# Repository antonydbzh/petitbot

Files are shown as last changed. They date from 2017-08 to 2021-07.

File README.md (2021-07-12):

# Le Petit Bot
1. Le Petit Bot c'est un robot, un programme, des logiciels pour commander Petit Bot et un programme pédagogique.
2. Le Petit Bot c'est un matériel facile à assembler par des jeunes à partir de 8 ans
3. Le Petit Bot ne coûte pas plus de 15 euros.
4. Un tutoriel détaillé est disponible sur [Wikidébrouillard](https://www.wikidebrouillard.org/wiki/Fabriquez_votre_PetitBot)

## Matériel
Le petit bot se compose :
* 2 servomoteurs à rotation continue
* 1 Wemos D1 Mini
* des fils dupont
* un système d'alimentation électrique (batterie 5V, support pour 4 piles AA - LR6,...).
* un interrupteur

En suite à vous de bricoler un plateforme, des roues, etc.
En carton, bouchon de bouteille, etc...

## Installation
L'installation de base consiste à changer le programme sur un wemos D1 mini avec l'IDE Arduino.
Puis de monter un robot à deux roues.
Puis, à la mise sus tension vous pouvez le controler via une page web à l'URL http://192.168.4.1
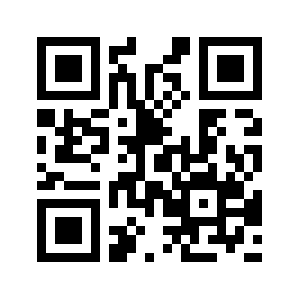
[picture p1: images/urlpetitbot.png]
QRCode de l'URL


## Usage
Le programme donne la capacité au petit bot d'être piloté depuis une page web.
il peut ainsi être piloté par [le logiciel SNAP! de l'Université de Californie à Berkeley](http://snap.berkeley.edu/).

## Contributing

1. Fork it!
2. Create your feature branch: `git checkout -b my-new-feature`
3. Commit your changes: `git commit -am 'Add some feature'`
4. Push to the branch: `git push origin my-new-feature`
5. Submit a pull request :D

## History

TODO: Write history

## Credits

Julien Rat - Les petits débrouillards
Antony Auffret - Les petits débrouillards
Et bien d'autres avant et après, un peu partout.
Ce programme est inspire de : http://www.esp8266.com/viewtopic.php?f=29&t=6419#sthash.gd1tJhwU.dpuf

## License

CC-By-Sa

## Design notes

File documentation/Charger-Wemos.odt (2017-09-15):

## Charger le programme sur le Wemos avec le logiciel Arduino

Pour programmer le wemos, nous utilisons le logiciel Arduino.

Nous devons ajouter quels outils complémentaires à ce logiciel pour deux raisons :

- Lui donner les capacité de gérer la carte Wemos D1 mini.
- Le doter de « bibliothèques » pour gérer le Wifi et les capteurs.

Attention en anglais le terme « librairies » est un faux-ami. Il se traduit par « bibliothèques ». Les bibliothèques sont des fichiers de code qu'il serait laborieux de retaper à chaque fois qu'on en a besoin.

### Ajouter les bibliothèques nécessaires

Pour le petit Bot nous avons besoin des bibliothèques suivantes :

- Servo.h

ATTENTION : Si il manque des bibliothèques, le logiciel Arduino refusera de charger le programme et renverra un message d'erreur. Ce message d'erreur vous indique quelle bibliothèque manque.

Pour installer les bibliothèques, il existe plusieurs manière. Le logiciel vous aide directement à installer les bibliothèques. Pour le cas ou certaines ne serait pas disponibles, essayez la seconde méthode.

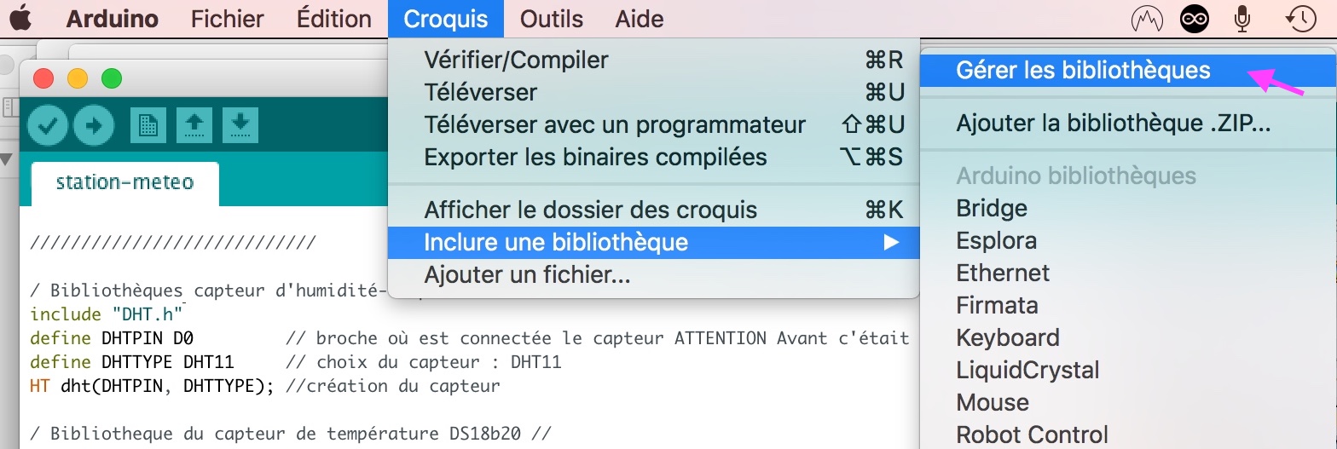
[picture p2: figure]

Commencez par celle-ci : ouvrez le logiciel Arduino puis allez dans Croquis → inclure une bibliothèque → gérer les bibliothèques

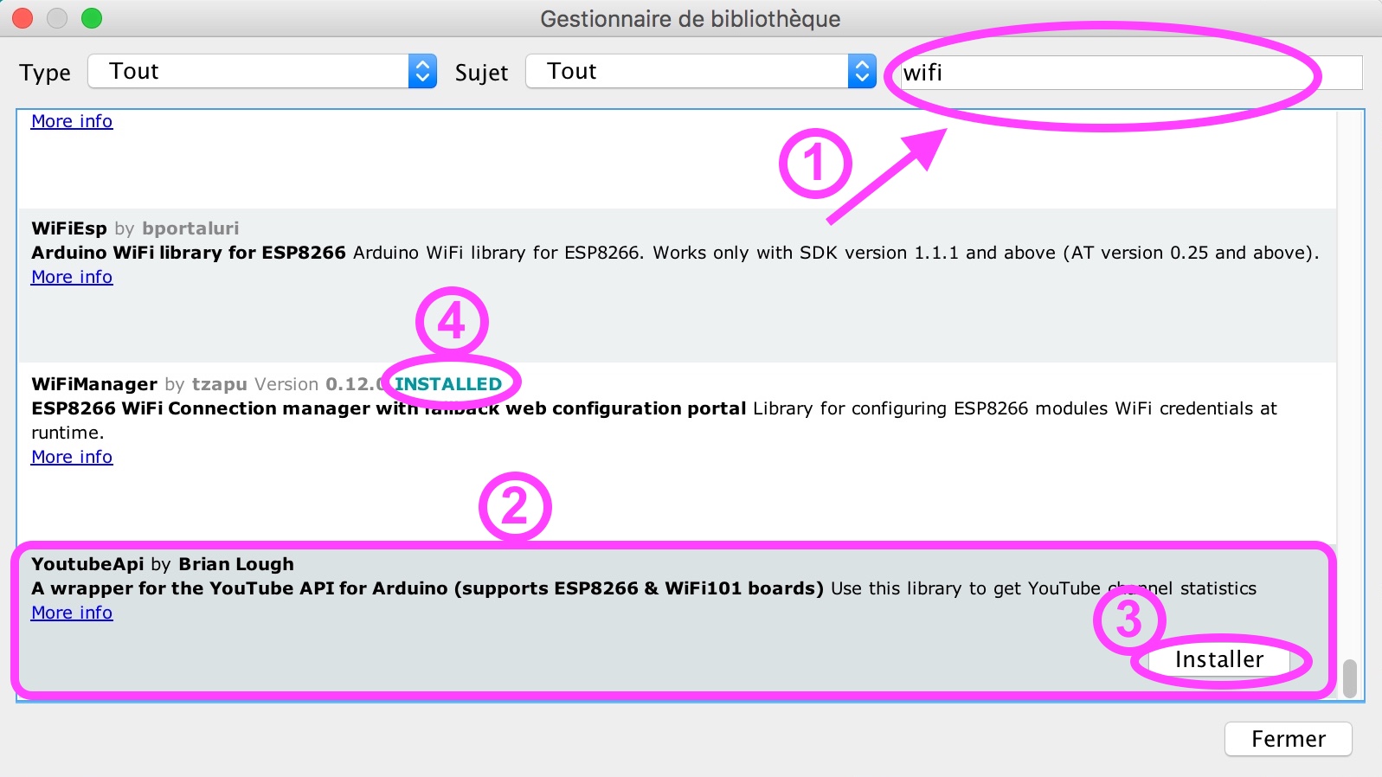
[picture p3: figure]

La fenêtre de gestion des bibliothèques s'ouvre :

1. Recherchez votre bibliothèque.
2. Cliquez la bibliothèque recherchée, « installer » apparaît.
3. Cliquez sur « installer »
4. Votre bibliothèque apparaît comme installée.

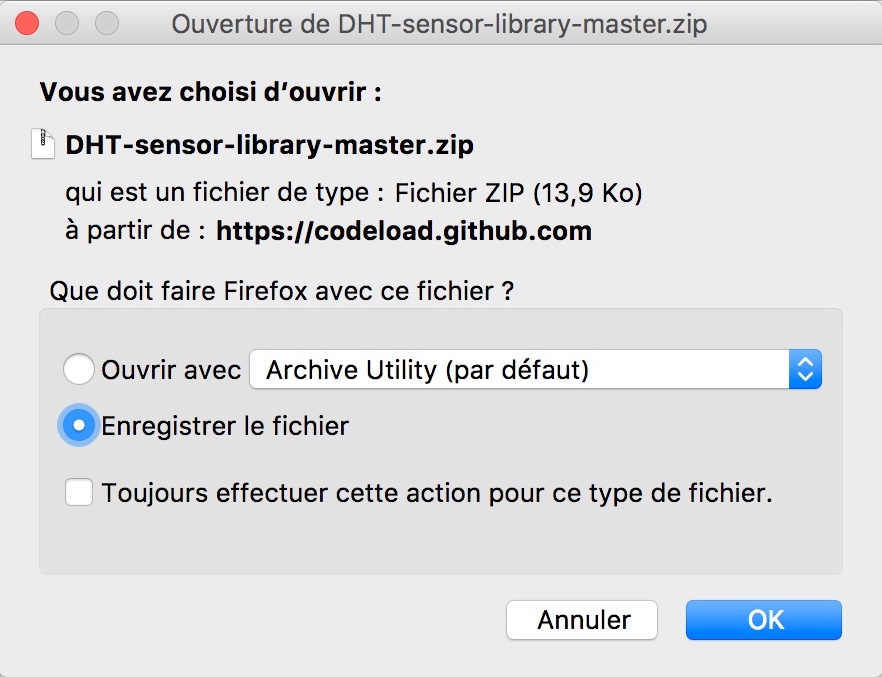
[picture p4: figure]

La seconde méthode :

Cliquez sur le lien donné plus haut pour télécharger la bibliothèque. Par exemple la bibliothèque qui permet de gérer les capteurs DHT.

https://github.com/adafruit/DHT-sensor-library/archive/master.zip

Votre navigateur vous propose de l'enregistrer, vous le faite, sur votre bureau par exemple.

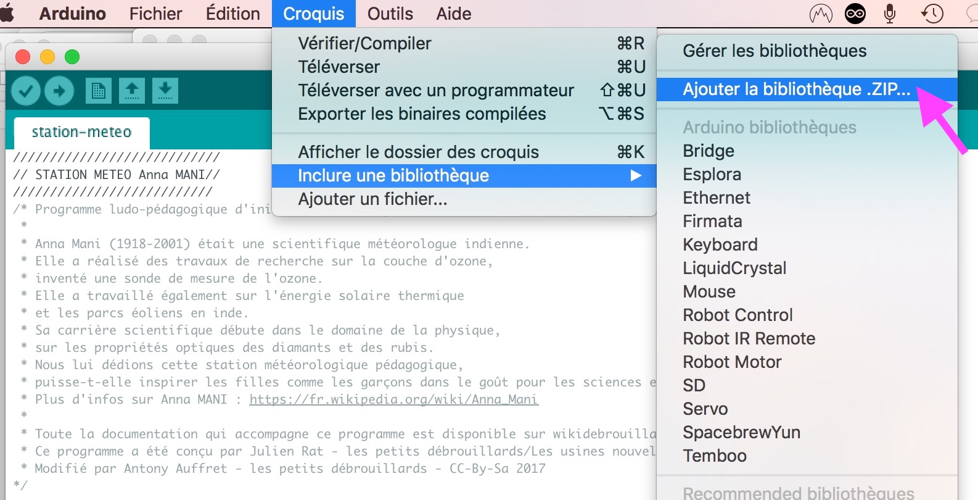
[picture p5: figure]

Ensuite, vous allez ajouter cette bibliothèque dans le logiciel Arduino.

Cliquez sur Croquis → inclure une bibliothèque → Ajouter la bibliothèque.ZIP

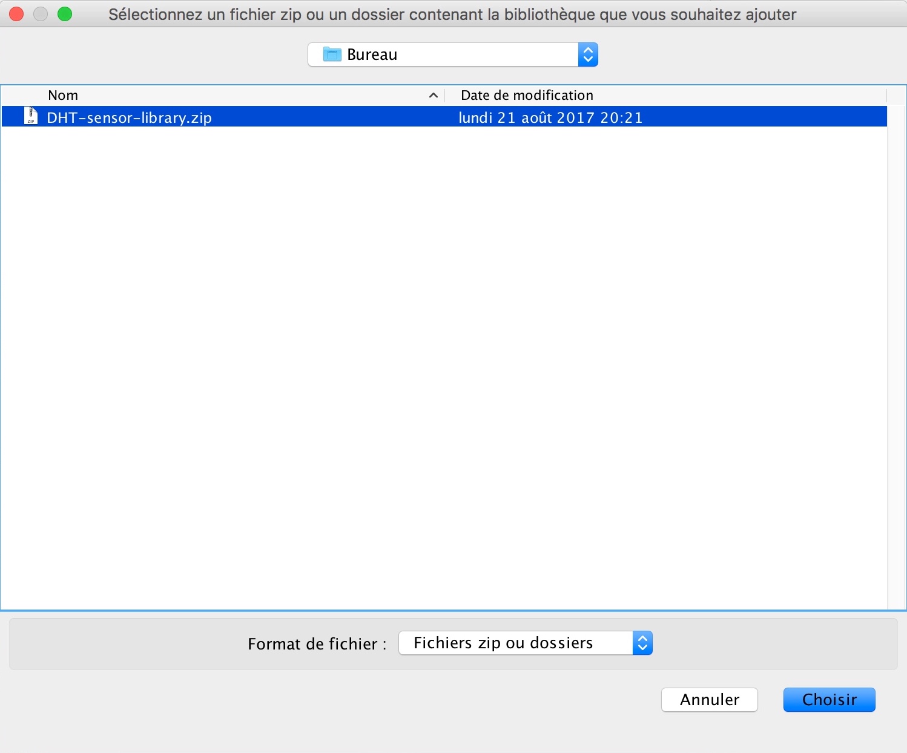
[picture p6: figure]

Une fenêtre de recherche s'ouvre.

Sélectionnez la bibliothèque, cliquez sur Choisir

C'est fait !

### Télécharger le programme sur le Wemos

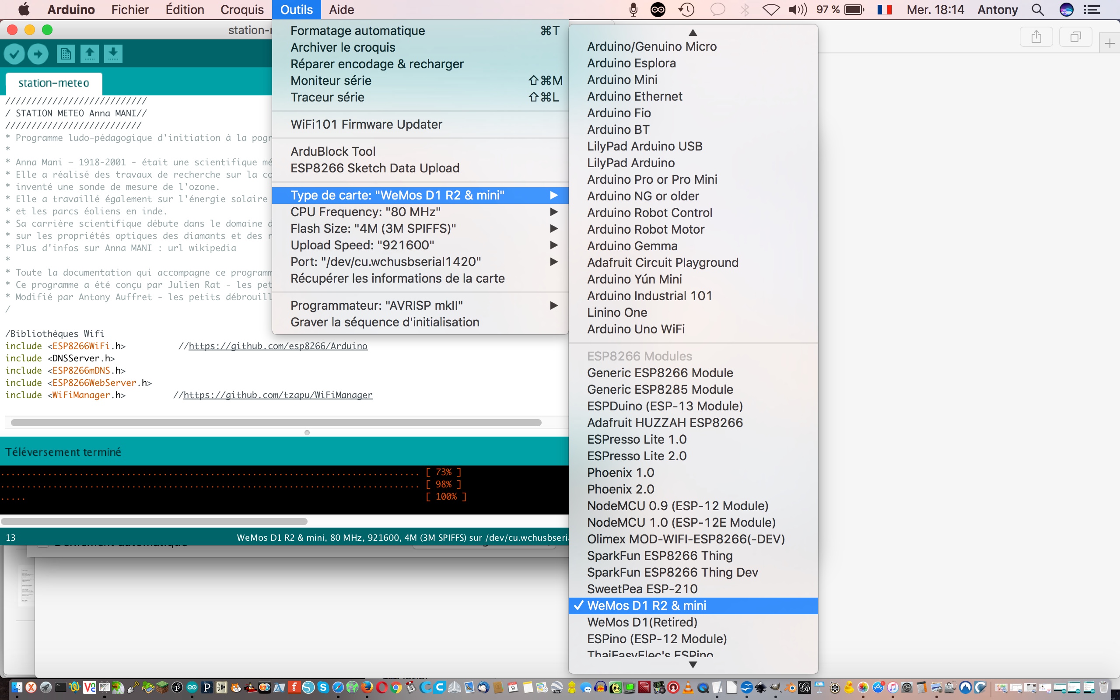
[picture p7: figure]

Ouvrez votre logiciel Arduino

Branchez le Wemos.

Choisissez le bon type de carte.

ATTENTION !

Il faut que vous ayez configuré le logiciel Arduino pour qu'il puisse gérer les cartes Wemos (Un tutoriel en se sens est disponible).

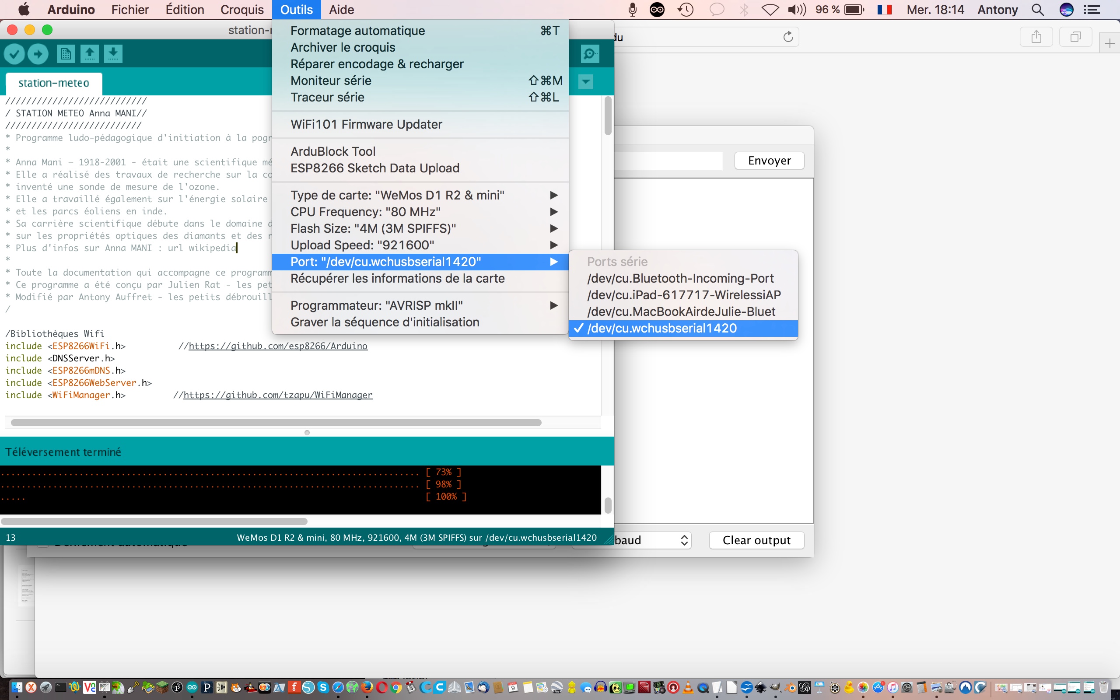
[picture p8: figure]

Choisissez le port.

Si le port du Wemos n'apparait pas, il y a plusieurs causes possibles :

- Les pilotes du Wemos ne sont pas installé.
- Le câble utilisé n'est pas bon (il existe des câbles USB-Micro USB qui ne font pas circuler les données (ceux des chargeurs simples par exemple)).

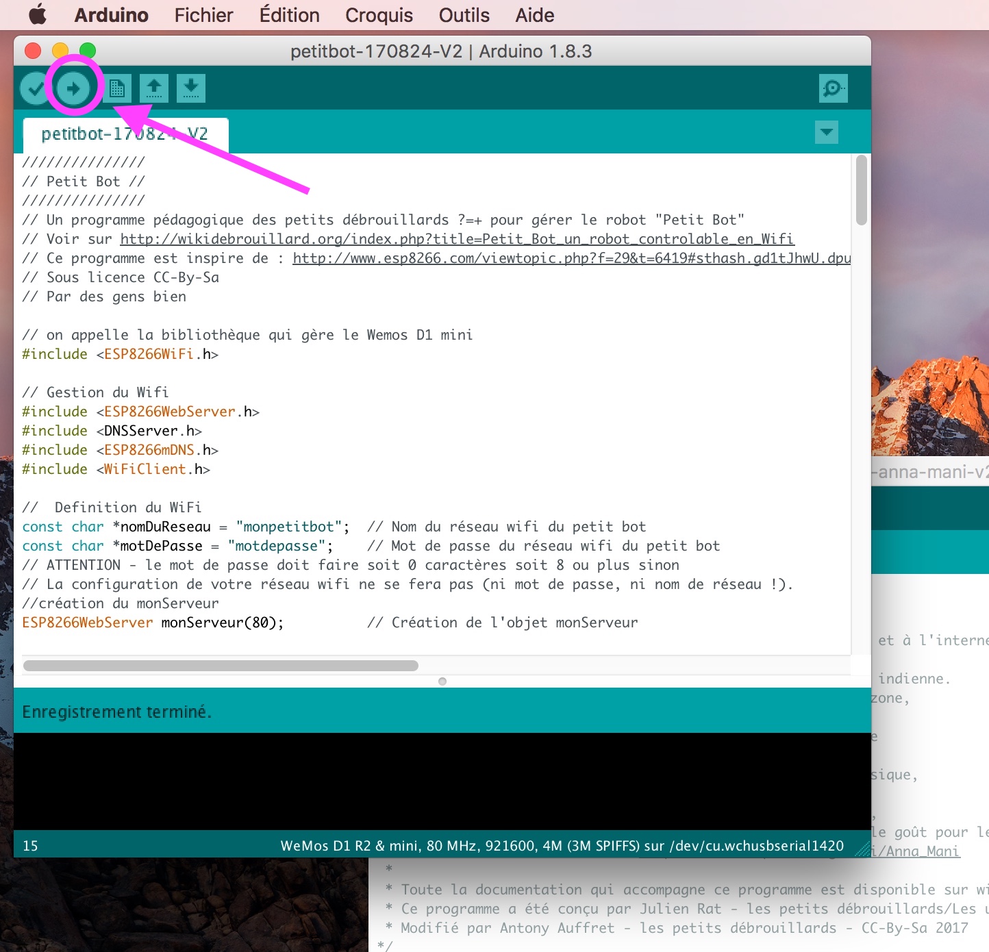
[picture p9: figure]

Téléversez le programme « petitbot » dans votre Wemos.

Si le téléchargement ne fonctionne pas essayez d'appuyer sur le bouton « reset » du Wemos.

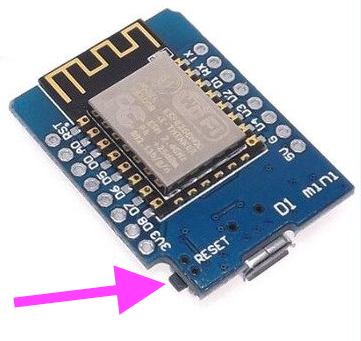
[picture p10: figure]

Une fois le programme chargé, le petit bot est prêt à servir.

Le petit Bot - 2017

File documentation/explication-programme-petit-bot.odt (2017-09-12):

//////////////////////

// Petit Bot //

//////////////////////

// Un programme pédagogique des petits débrouillards ?=+ pour gérer le robot "Petit Bot"

// Voir sur http://wikidebrouillard.org/index.php?title=Petit_Bot_un_robot_controlable_en_Wifi

// Ce programme est inspire de : http://www.esp8266.com/viewtopic.php?f=29&t=6419#sthash.gd1tJhwU.dpuf

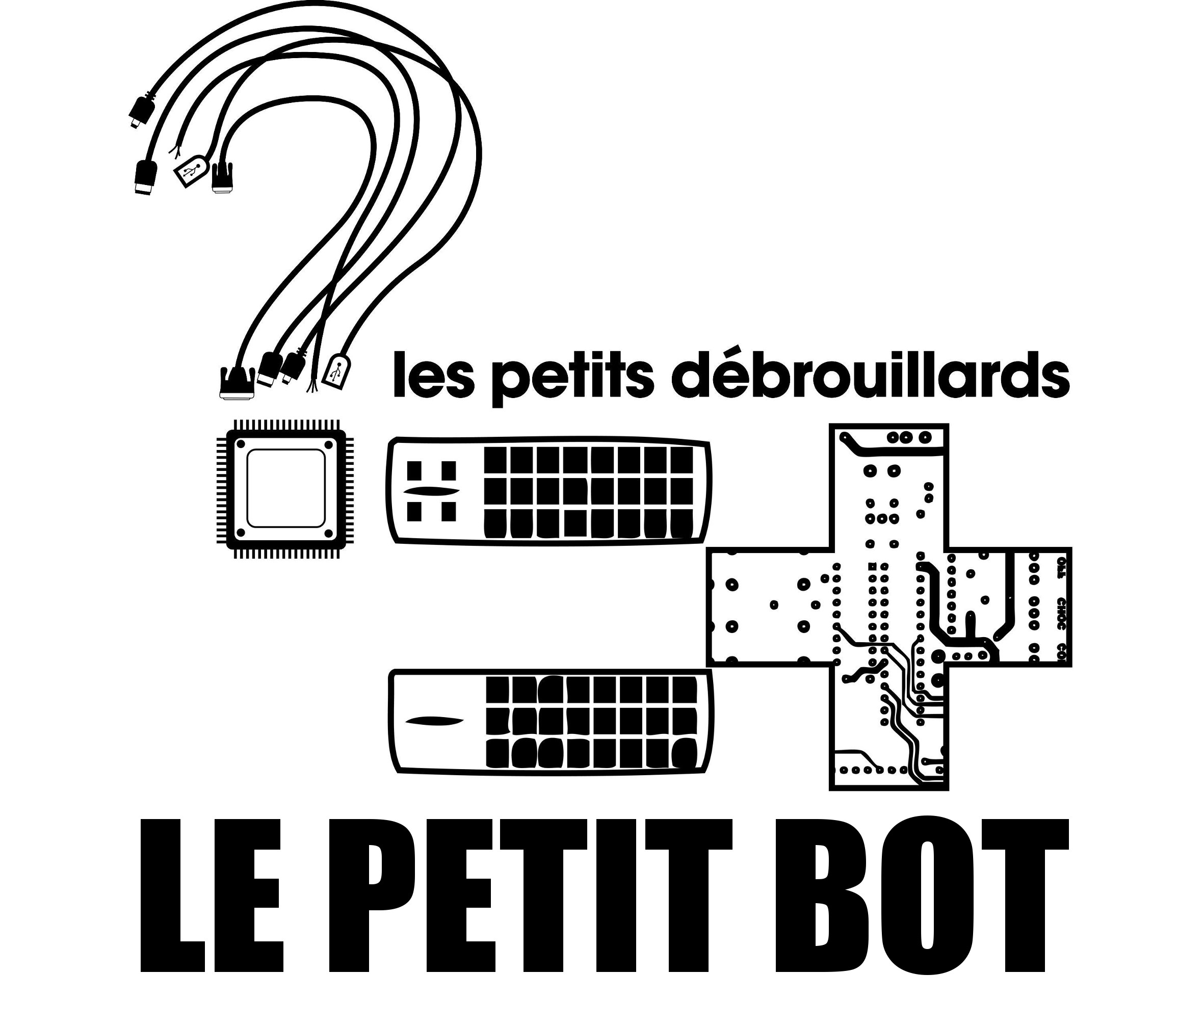
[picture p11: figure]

// Sous licence CC-By-Sa

// Par des gens bien

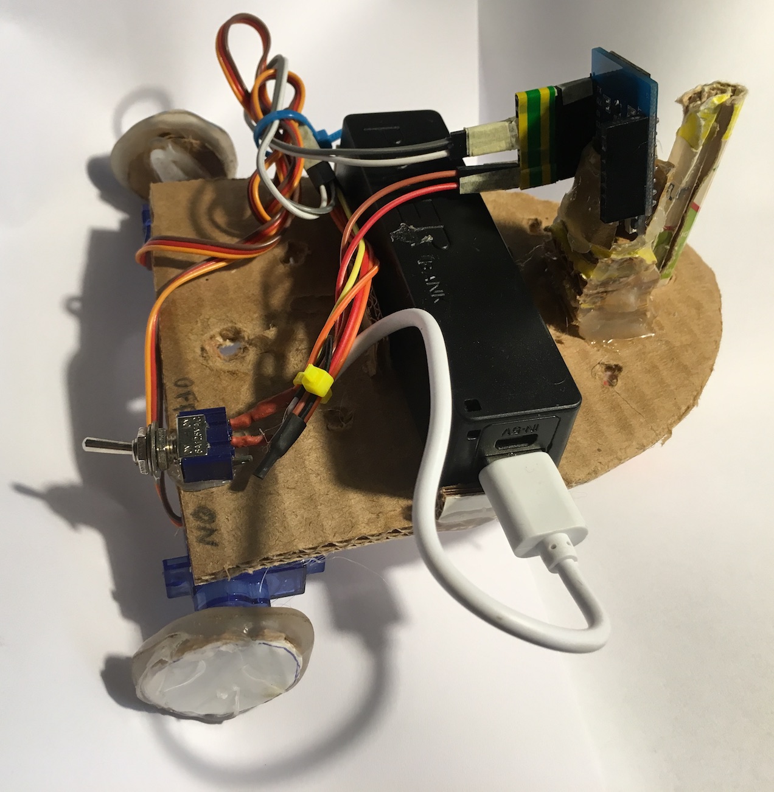
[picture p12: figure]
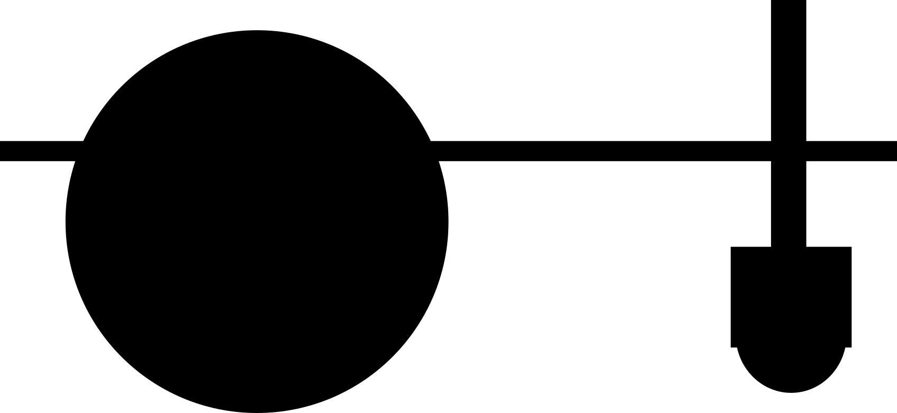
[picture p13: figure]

/////////////////////////////////////////DECLARATIONS/////////////////////////////////

// on appelle la bibliothèque qui gère le Wemos D1 mini

#include <ESP8266WiFi.h>

// Gestion du Wifi

#include <ESP8266WebServer.h>

#include <DNSServer.h>

#include <ESP8266mDNS.h>

#include <WiFiClient.h>

// Definition du WiFi

const char *nomDuReseau = "petitbot"; // Nom du réseau wifi du petit bot

const char *motDePasse = "mot-de-passe"; // Mot de passe du réseau wifi du petit bot

// ATTENTION - le mot de passe doit faire soit 0 caractères soit 8 ou plus sinon ça marche pas

//création du serveur

ESP8266WebServer monServeur(80); // Création de l'objet « monServeur »

//Gestion des servomoteurs

#include <Servo.h> // Appel de la bibliothèque qui gère les servomoteurs

Servo servogauche; // Déclaration du servo qui gère la première roue

Servo servodroit; // Seconde roue

// Déclaration des Variables

//int --- en cours, partie du programme en cours de développement

int val = -1; // La variable « val » nous sert à stocker la commande de l'utilisateur (stop, avance, ...).

//////////////////////////INITIALISATION DU PROGRAMME////////////////

(n'est fait qu'une seule fois)

void setup(){

delay(1000);

Serial.begin(9600); // Ouvre une connexion série pour monitorer le fonctionnement du code quand on reste branché a l'ordinateur

Serial.println();

Serial.println();

configDuWifi();

configDuServeur() ;

monServeur.begin() ;

servodroit.detach(); // Place les servos hors tension

servogauche.detach();

pinMode(LED_BUILTIN, OUTPUT); // met la led du Wemos en sortie

digitalWrite(LED_BUILTIN, LOW); // met la led du Wemos sur le niveau bas ce qui l'allume.

pinMode(LED, OUTPUT);

digitalWrite(LED, HIGH);

}

/////////////////////////BOUCLE PRINCIPALE//////////////////////////////

(se répète indéfiniment)

void loop(){

val = -1;

monServeur.handleClient(); // Le serveur « monServeur » attend la connexion des navigateurs

}

///////////////////////GESTION DES INSTRUCTIONS////////////////////////

void configDuServeur() {

monServeur.on("/avance", HTTP_GET, []() { // Si clic sur l'URL « http://192.168.4.1/avance »

val = 1; // alors val = 1, c'est pour les conditions de la fonction « redactionPageWeb »

Serial.println("avance"); // Ecrit sur le moniteur série « avance »

redactionPageWeb(); // Appelle la fonction « redactionPageWeb »

});

monServeur.on("/recule", HTTP_GET, []() {

val = 2;

Serial.println("recule");

redactionPageWeb();

});

monServeur.on("/droite", HTTP_GET, []() {

val = 4;

Serial.println("droite");

redactionPageWeb();

});

monServeur.on("/gauche", HTTP_GET, []() {

val = 3;

Serial.println("gauche");

redactionPageWeb();

});

monServeur.on("/stop", HTTP_GET, []() {

val = 0;

Serial.println("stop");

redactionPageWeb();

});

monServeur.on("/", HTTP_GET, []() {

val = -1;

redactionPageWeb();

});

}

///////////////////////////LA PAGE WEB DE CONROLE DU PETIT BOT//////////////////////////////

void redactionPageWeb(){

// Prépare la page web de réponse (le code HTML sera écrit dans la chaine de caractère "pageWeb").

String pageWeb = "<!DOCTYPE HTML>\r\n";

pageWeb += "<html>\r\n";

pageWeb += "<center>"; // On ouvre la balise qui va centrer les boutons

pageWeb += "<h1 style=\"font-size:300%;\"\> Le petit bot ";

pageWeb += "<style type=\"text/css\"> body { color: #212121; background-color: #CC0C59 } </style>";

// On finalise l'écriture de la page Web et on donne les instructions aux servos

pageWeb += instruction(val); // pour cela on appelle la fonction "instruction" en lui envoyant « val »

// On termine l'écriture de la page Web

pageWeb += "</h1>";

pageWeb += "<br>"; //aller à la ligne

pageWeb += "<br>"; //aller à la ligne

pageWeb += "<a href=\"/stop\"\"><button style=\"font-size:200%; width: 18%; background-color:#0CCC16; border-radius: 12px\"\>Stop </button></a>\r\n"; // créer un bouton "Stop", qui envoie sur l'URL /stop

pageWeb += "<a href=\"/avance\"\"><button style=\"font-size:200%; width: 18%; background-color:#0CCC16; border-radius: 12px\"\>Avance </button></a>\r\n"; // créer un bouton "Avance"...

pageWeb += "<a href=\"/recule\"\"><button style=\"font-size:200%; width: 18%; background-color:#0CCC16; border-radius: 12px\"\>Recule </button></a>\r\n";

pageWeb += "<a href=\"/droite\"\"><button style=\"font-size:200%; width: 18%; background-color:#0CCC16; border-radius: 12px\"\>Droite </button></a>\r\n";

pageWeb += "<a href=\"/gauche\"\"><button style=\"font-size:200%; width: 18%; background-color:#0CCC16; border-radius: 12px\"\>Gauche </button></a><br />\r\n";

pageWeb += "</center>"; // tout est centré sur la page

pageWeb += "</html>\n"; // Fin de la page Web

// On envoie la page web

server.send(200, "text/html", pageWeb);

delay(1);

}

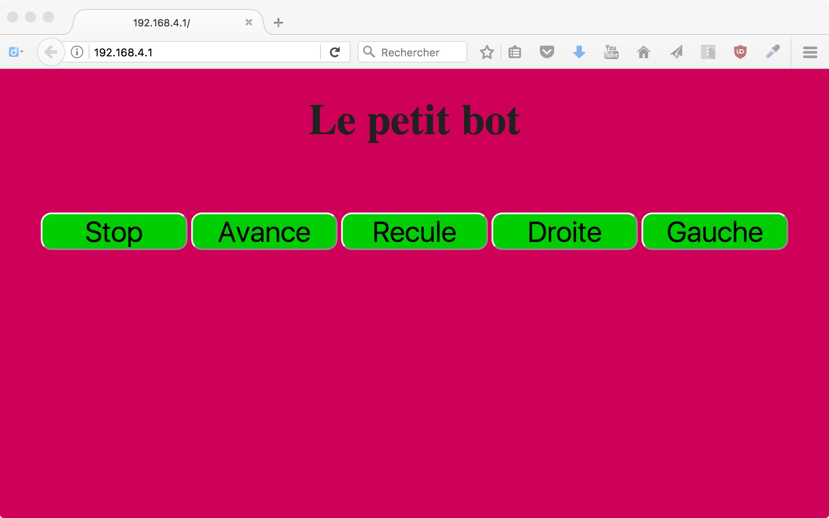
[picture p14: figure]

///////////////////INSTRUCTIONS////////////////////////////////

String instruction(int valeur){ // Cette fonction traite les instructions envoyées par la donnée « val » placée dans la variable local « valeur » et renvoie une chaine de caractère « completePage ».

int gauche; // Variable dont la valeur fait tourner le servo gauche

int droite; // Idem pour le servo droit

String completePage; // Déclaration de la chaine de caractère qui sera renvoyée par cette fonction pour compléter la page web

switch(valeur){ // En fonction de la variable valeur on va donner un ordre aux servos

case 0 : // et un texte à la chaine de caractère "completePage"

completePage = " est a l&rsquo;arr&ecirc;t ";

droite = 90; // immobile

gauche = 90;

break;

case 1 :

completePage = " avance ";

droite = 180; // Tourne dans le sens des aiguille d'une montre

gauche = 0; // dans l'autre sens

break;

case 2 :

completePage = " recule ";

droite = 0;

gauche = 180;

break;

case 3 :

completePage = " tourne a gauche ";

droite = 180;

gauche = 180;

break;

case 4 :

completePage = " tourne a droite ";

droite = 0;

gauche = 0;

break;

}

servogauche.attach(D1); // Broche D1

servodroit.attach(D2); // Broche D2

servogauche.write(gauche);

servodroit.write(droite);

return completePage; // on renvoie la chaine de caractère pour compléter la page web

}

////////////////////////CONFIGURATION WIFI//////////////////////////////

void configDuWifi(){ // Fonction de configuration du Wifi

WiFi.mode(WIFI_AP); // le wemos est en mode "Point d'Accès" (il déploie un réseau wifi)

WiFi.softAP(nomDuReseau, motDePasse, 2); // on démarre le "Point d'Accès".

MDNS.begin(nomDuReseau); // gérer les DNS ce qui rendra votre petit bot accessible

MDNS.addService("http", "tcp", 80); // via http://nomDuReseau.local

IPAddress monIP = WiFi.softAPIP(); // on récupère l'adresse IP du petit Bot

Serial.print("Adresse IP de ce Point d'Accès : ");

Serial.println(monIP); // on l'écrit sur le moniteur série

return; // on retourne à l'endroit ou la fonction a été appelée.

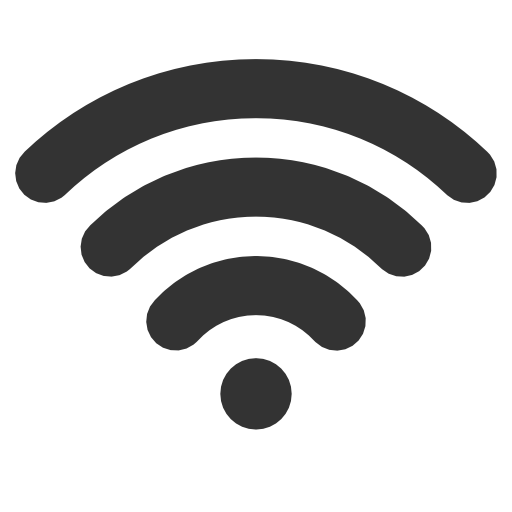
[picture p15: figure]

}

Le petit Bot, le code ! – Les petits débrouillards 2017 – page 8 sur 10

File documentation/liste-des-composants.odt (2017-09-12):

Les composants

du petit Bot

Liste des composants

1. Wemos D1 Mini
2. 2 servomoteurs

Pour l'alimentation électrique, il y a plusieurs options :

1. Option boitier à piles avec interrupteur intégré.
2. Option batterie 5V rechargeable avec interrupteur supplémentaire
3. Option boitier à pile qu'on fabrique soi-même avec interrupteur supplémentaire
4. Option alimentation séparée pour les servomoteurs et le wemos.

Il existe également des extensions dont nous pouvons doter le petit bot :

1. 2 LEDs
2. 3 servomoteurs
3. Un capteur de distance
4. un mini-écran

Description des capteurs et actionneurs

nom | Photo | Pictogramme | description

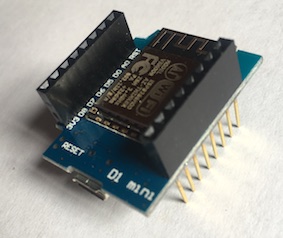
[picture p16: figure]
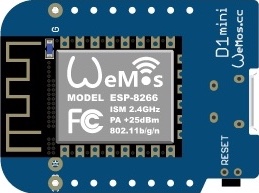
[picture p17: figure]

Wemos D1 Mini | | | Voir les détails sur http://www.wemos.cc Nous avons choisis de lui souder ses longues pattes avec broches pour ne pas perdre de possibilité de branchement lorsqu'il est installé sur la plaque de prototypage

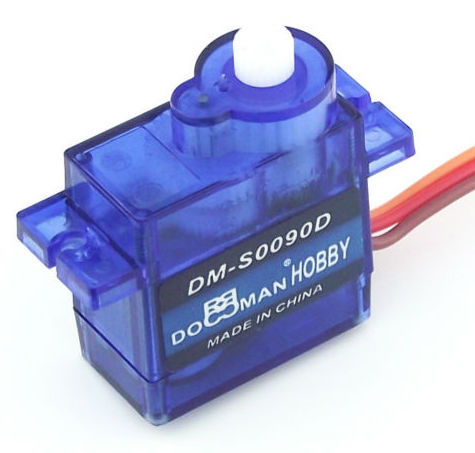
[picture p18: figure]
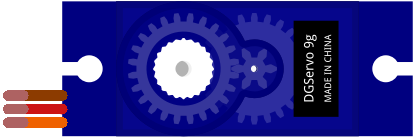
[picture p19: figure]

Servomoteur à rotation continue. | | | Les servomoteurs classique sont pilotable. On peut les orienter de 0 à 90° ou 180°, ou autre, jusqu'à 360° maximum. Techniquement c'est potentiomètre rotatif qui est sur l'axe du moteur, lui permettant ainsi de connaître sa position. Un servomoteur à rotation continue n'a pas de potentiomètre. Il va tourner perpétuellement. - 0° : tourne à gauche à fond - 180° : tourne à droite à fond - 90 ° : stop il est possible de gérer la vitesse. Plus lentement près de 90°

Alimentation électrique :

Plusieurs options disponibles

nom | Photo | Pictogramme | description

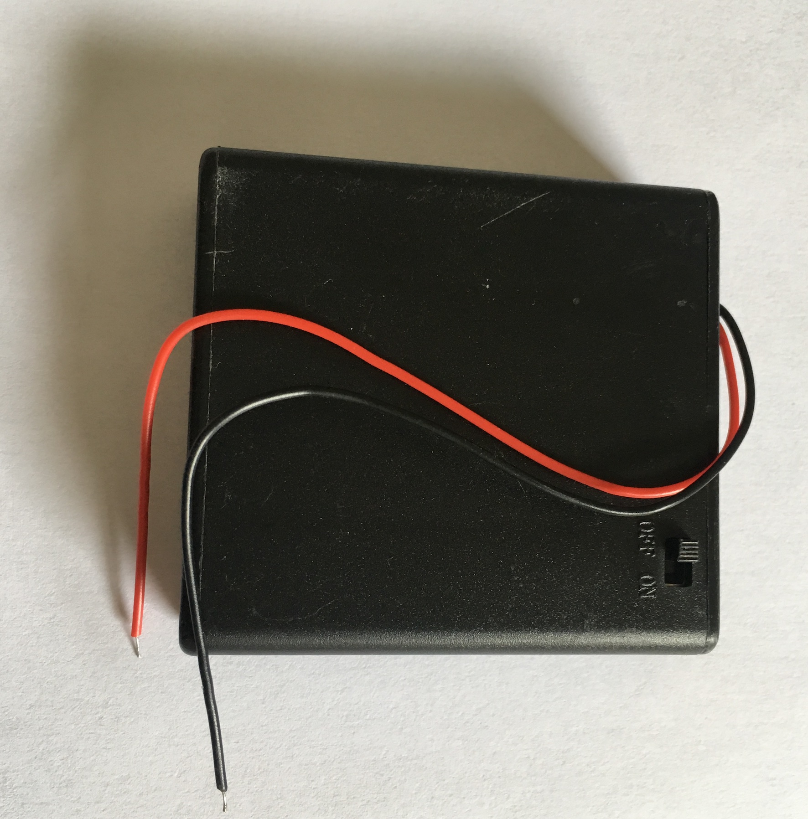
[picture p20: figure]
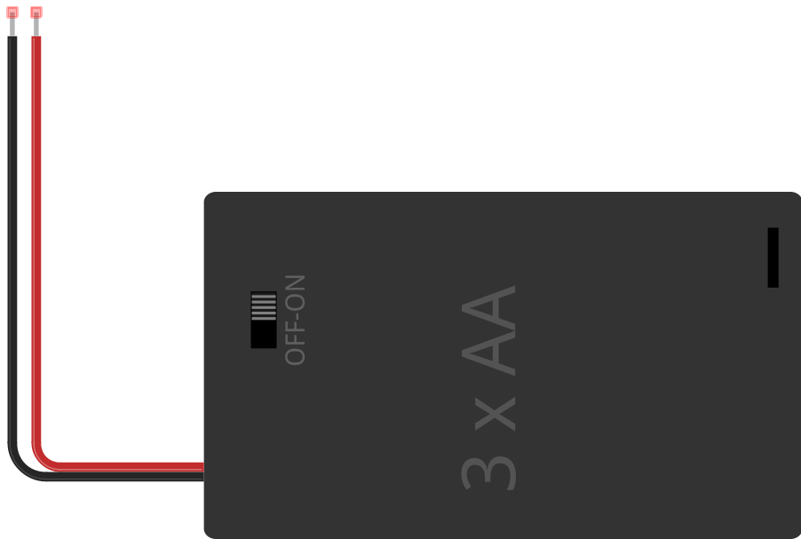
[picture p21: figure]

Boitier à piles avec interrupteur intégré. | | | Il s'agit d'un boitier tout fait, équipé d'un interrupteur ; c'est fiable et pas très cher.

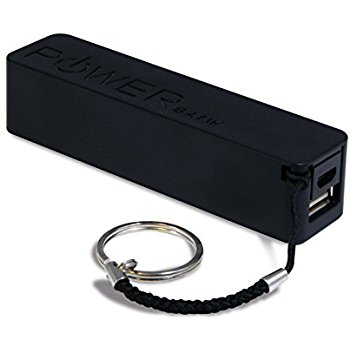
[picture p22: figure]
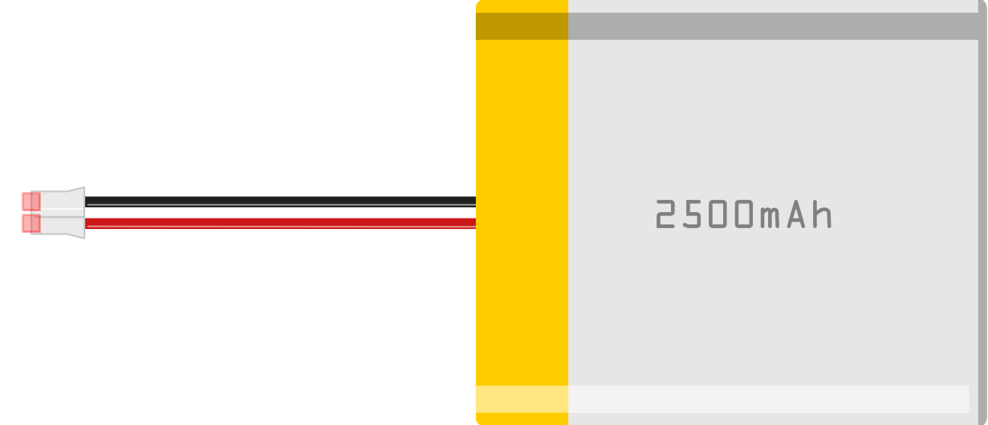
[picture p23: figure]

Batterie 5V rechargeable | | | Existe en format brut, il faudra un peiu d'éelctronique pour la recharger. Sinon (photo) une batterie portable pour recharger les téléphones en encore mieux.

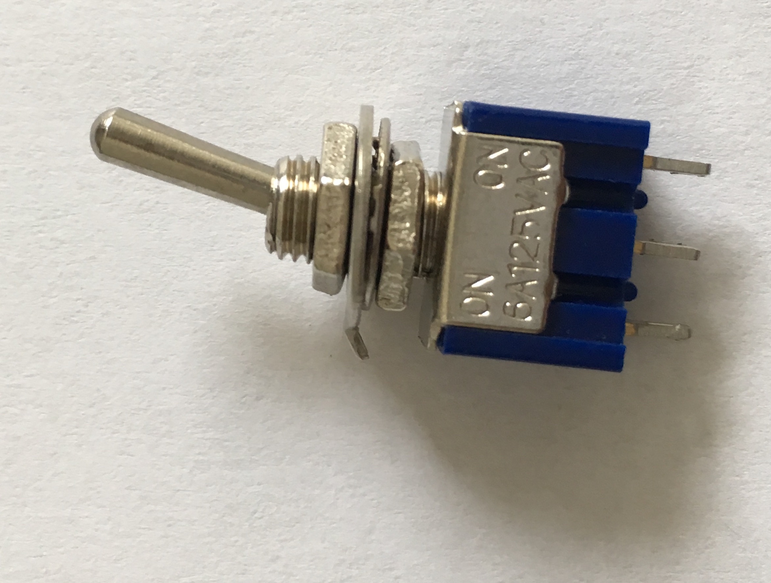
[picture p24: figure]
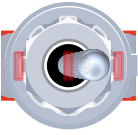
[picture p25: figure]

interrupteur supplémentaire | | | Cet interrupteur à bascule possède 3 broches. Il les connecte deux à deux. On le dit on-on.


Boitier à pile qu'on fabrique soi-même | | | Il y a probablement beaucoup de manière de réaliser un boitier à piles. Ici avec une imprimante 3D, il faudra compléter la forme imprimer avec un peu de câblage électrique. Source, sur Thingiverse : https://www.thingiverse.com/thing:1132839


Alimentation séparée pour le Wemos : pas plus de 5V (ici 2 piles). | | | Il s'agit d'un boitier tout fait, sans interrupteur celui-ci. C'est fiable et pas très cher.


Alimentation séparée : pour les servomoteurs : 6V (4X1,5V). | | | cf plus haut

Extensions pour le petit Bot :

nom | Photo | Pictogramme | description


LED | | | Light Emitting Diode – Diode Électro-Luminescente en français soit DEL. Elle ne laisse passer le courant que dans un sens en émettant de la lumière


Plaque de prototypage | | | 10X17 soient 170 trous. Les trous sont connectés ensemble en deux rangées parallèle de 17 lignes de 5 trou.


Cable USB ↔ microUSB | | | Permet soit d'alimenter le Wemos, soit de le connecter à un ordinateur


Capteur de distance HC-SR04 | | | Permet de mesurer la distance avec des ultrasons.


3 servomoteurs | | | Pour doter le petit bot d'un bras articulé avec une pince. Ces servomoteurs de 9g sont contrôlable de 0° à 180°. `


Ecran Oled 128X64 pixels | | | Permet d'afficher en monochrome ou bicolore (suivant le modèle) des image et du texte.

Le budget détaillé avec les liens vers les achats en ligne est disponible sur le Github du projet.

Le petit bot - 2017

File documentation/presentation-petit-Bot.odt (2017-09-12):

Le petit Bot


Un robot bidouillable polymorphe,

pilotable par smartphone


# De quoi s'agit-il ?

C'est un robot bidouillable très simple qu'on piloter avec un navigateur web (Firefox, safari, chrome...).

Il est composé de 2 servomoteurs à rotation continue, une alimentation et un microcontrôleur capable de déployer un réseau Wifi, le Wemos D1 mini.

Bidouillable ? Polymorphe ?

Pour faire les roues ? Le châssis ? Pour fabriquer l'alimentation ?

Vous pouvez imaginer, bidouiller, bricoler et inventer des variantes créatives, certains en ont même fait un bateau !

Carton, colle, cutter ?

- Le champ des possibles vous est ouvert, la récup' est votre caverne d'Ali Baba.


Avec une imprimante 3D ?

vous pouvez réaliser tout ou partie du châssis et des différentes parties :

- support de bille pour roue avant


- boitier pour les piles (2, 3 ou 4 piles).
- Roues


- châssis en entier.

Avec une découpeuse laser ?

- Châssis,
- roues,
- boitier à piles

Des extensions ?

- Bras robotisé,
- LED comme gyrophare ou comme clignotant,
- capteur de distance,
- écran pour lui donner des émotions,...

Le petit Bot - 2017

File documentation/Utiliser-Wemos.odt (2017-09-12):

Utiliser la Carte

Wemos D1 mini

Cette petite carte est livrée en kit pour une utilisation variée :

- Souder fils et composants directement sur la carte, pour des montage définitifs.
- Souder des broches femelles simples.
- Souder des broches malles simples, pour brancher la carte sur une plaque de prototypage.
- Souder des broches femelles traversantes pour allier le coté pratique des deux.


### Une petite manip' pour utiliser le logiciel Arduino avec le Wemos D1 Mini :

1 - Pour mac et windows, il faut installer les pilotes (drivers) téléchargeable ici : https://wiki.wemos.cc/downloads

Sur Linux, prenez bien soin de vérifier que votre version du logiciel est récente.

2 – Ensuite, il faut ajouter la carte au logiciel Arduino. Pour cela allez dans les « Préférences » d'Arduino, ajoutez l'URL suivante dans « URL de gestion de cartes supplémentaires » :

http://arduino.esp8266.com/stable/package_esp8266com_index.json


Puis, cliquez sur outils → Type de carte → Gestionnaire de carte.


Là, l'interface de gestion des cartes s'ouvre, tapez dans la recherche « esp8266 ».

Cliquez sur « esp8266 By ESP8266 Community » puis sur « Installer ».


Le logiciel Arduino est prêt à gérer votre carte Wemos D1 mini !

Vous retrouvez ces consignes sur le Wiki du Wemos : https://wiki.wemos.cc/products:d1:d1_mini

AVERTISSEMENT :

Les sources de dysfonctionnement sont nombreuses. Mais ne vous découragez pas. Il faut être persévérant et vous apprendrez à résoudre les problèmes rencontrés.

La bidouille informatique n'est ni évidente, ni facile. Elle est exigeante en terme de rigueur et de complexité.

En prenant le temps d'apprendre et pratiquer, on acquière une bonne autonomie assez rapidement.

SOURCES D'ERREUR ET SOLUTIONS

Symptôme | Idée de solution
Impossible d'installer le « esp8266 By ESP8266 Community » | Vérifier qu'il y a bien quelque chose au bout de l'URL http://arduino.esp8266.com/stable/package_esp8266com_index.json Il est arrivé que ce soit indisponible.
Votre ordinateur plante quand vous branchez le Wemos (Kernel Panic sous mac par exemple). | Il faut installer les pilotes → https://wiki.wemos.cc/downloads


Le logiciel Arduino vous renvoie l'erreur : error: espcomm_open failed error: espcomm_upload_mem failed | C'est un problème de communication entre l'ordinateur et le wemos. Les causes peuvent être multiples : Vérifiez le branchement de votre wemos en USB à l'ordinateur. Vérifiez que votre câble USB → MicroUSB est bien un câble qui transfère les données (certains servent juste à charger les téléphones). Changez de câble USB → MicroUSB.


Impossible de charger le programme sur le wemos. | Pressez le bouton « reset » pendant quelques secondes lorsque le wemos est branché à votre ordinateur.

## En savoir plus sur le Wemos D1 mini

Le Wemos D1 mini est basé sur l'esp8266. Il s'agit, comme l'Arduino, d'un microcontroleur. Il est doté en plus du wifi.

Il existe beaucoup d'autres cartes basées sur l'esp8266.

On peut programmer le Wemos D1 mini de différente manière. Il nous intéresse car on peut l'utiliser comme un Arduino, avec le même logiciel.

Ce que sait faire le Wemos est remarquable :

- C'est une sorte d'Arduino.
- Il peut se connecter en wifi à une box, à un ordinateur, à l'internet, à un autre Wemos.
- Il peut être un simple « client », c'est à dire consulter des informations sur internet, interroger des serveurs,...
- Il peut être serveur, c'est à dire envoyer des informations, répondre à des requêtes, servir des pages web. Et on peut interagir avec le Wemos par ce biais.
- Il peut être point d'accès wifi.

Pour un utilisateur débutant, la principale différence entre l'Arduino et le Wemos ce sont les broches. Il n'y a qu'une broche analogique sur le Wemos ( 6 pour Arduino), 11 broches numériques sur le wemos (14 pour Arduino). Le Wemos fonctionne en 3,3V. Il faut veiller à ne jamais envoyer plus de 3,3V dans ses broches au risque de le détruire.

Equivalence des broches entre Wemos D1 mini et Arduino :


On peut l'acheter pour moins de 3€ sur le site chinois Aliexpress.

En savoir plus :

Wikidebrouillard : http://wikidebrouillard.org/index.php?title=Wemos_D1_mini

Wikipédia : https://fr.wikipedia.org/wiki/ESP8266

En anglais, le wiki du fabricant : https://wiki.wemos.cc/products:d1:d1_mini

Le Petit Bot - 2017

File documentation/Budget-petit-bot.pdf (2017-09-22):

BUDGET du PETIT BOT.

## Version avec une batterie rechargeable

désignation | quantité prix livraison incluse prix unitaire
| 400 | 10,16 € | 0,51 €
| 20 | 11,46 € | 0,57 €
bobines de fils électrique | 2 | 4,74 € | 0,24 €
interrupteurs | 20 | 3,98 € | 0,20 €
Plaques de prototypage | 10 | 3,25 € | 0,33 €
Plaques de prototypage | 10 | 3,26 € | 0,33 €
batterie | 20 | 88,00 € | 4,40 €
Servomoteurs | 40 | 134,86 € | 6,74 €
| 20 | 49,24 € | 2,46 €
TOTAL | | 308,95 € | 15,77 €
Soient | 15,45 €par petit bot, pour 20

cables dupont - « jumper » - male-male Cables USB Data

wemos D1 Mini

BUDGET du PETIT BOT.

## Version avec une batterie rechargeable

## liens

https://fr.aliexpress.com/item/40pcs-dupont-cable-jumper-wire-dupont-line-male-to-male-dupont-line-20cm-1P-diameter-2/32481603887.htmlhttps://fr.aliexpress.com/item/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

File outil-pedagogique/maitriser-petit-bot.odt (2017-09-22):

## Maîtriser le petit Bot.

Avant toute chose, il est nécessaire de comprendre comment fonctionne le petit bot, rien de tel que de préparer un petit jeu à plusieurs.

Matériel :

- 1 petit bot version basique
- 5 ordinateurs / téléphones / tablettes
- 5 « pilotes » qui seront chargés de collaborer pour piloter le petit bot
- 5 fiches actions (Avance / Recule / Gauche / Droite / Stop) avec la requête correspondante au dos
- 1 but « le petit bot doit se rendre à tel endroit »
- un tableau, une craie de quoi écrire en groupe

Déroulement :

On allume et positionne le petit bot à un endroit de la salle, puis on énonce la consigne :

« le petit bot doit se rendre à tel endroit de la salle ».

On distribue les fiches actions aux participants.

On invite les participants à se connecter au wifi du petit bot et à tester les différentes commandes inscrites sur les fiches pendant un temps donné

On remet le petit bot en position initiale, et on reprend l’objectif principal « le petit bot doit se rendre à tel endroit de la salle».

En fin d’activité, on demande aux participants de lister les différentes commandes utilisées pour remplir l’objectif sur le tableau. Ils auront ainsi réalisé un premier programme permettant de programmer le petit bot.

Cette activité est à améliorer !

Le petit Bot - 2017

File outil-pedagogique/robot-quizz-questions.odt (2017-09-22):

QUESTION :

Quelle est la planète sur laquelle ne vivent que des robots ?

REPONSE :

Mars : plusieurs robots y vivent. Le robot Mars 3 est arrivée en 1971, les sondes viking 1 et 2 atterrissent en 1976. Pathfinder l'atterisseur de Sojourner est lui arrivé en 1997. Spirit et Opportunity en 2004. Curiosity en 2012. D'autres projet sont en en cours. Il y a bien d'autres robots sur Mars mais hélas, ils se sont écrasés à l'amarsissage !

QUESTION :

D'ou vient le mot robot ?

REPONSE :

R. U. R. (Rossum's Universal Robots), sous-titre en anglais du livre tchèque Rossumovi univerzální roboti, est une pièce de théâtre de science-fiction, écrite en 1920 par Karel Čapek (né en Tchécoslovaquie), mise en scène à Prague en 1921 et jouée à New York en 1922. C'est dans cette pièce que l'auteur utilisa le mot robot pour la première fois, bien que ce soit son frère Josef qui l'ait inventé à partir du tchèque robota qui signifie « corvée » – rob veut dire « esclave » en slave ancien, aujourd'hui encore rabotat veut dire « travailler » en russe et robotnik signifie « ouvrier » en slovaque et en polonais. Robot supplanta immédiatement le terme automaton utilisé par l'auteur dans la courte pièce Opilec de 1917.

QUESTION :

Quelle est la définition d'un robot ?

REPONSE :

Un robot est un dispositif mécatronique (alliant mécanique, électronique et informatique) conçu pour accomplir automatiquement des tâches imitant ou reproduisant, dans un domaine précis, des actions humaines. La conception de ces systèmes et l'objet d'une discipline scientifique, branche de l'automatisme nommé robotique.

On élargit le sens du mot robot à des machines telles que les lave-vaisselle, lave linge, voiture autonomes ou encore des logiciels qui effectuent des taches automatiques (écriture d'articles de presse, scan d’internet pour l'indexation par les moteurs de recherche, logiciels qui corrigent Wikipédia, etc...).

QUESTION :

Quand les robots industriels sont-il apparus ?

REPONSE :

Dans le début des années 1970. Ils sont destinés à exécuter certaines tâches répétitives, éprouvantes ou toxiques pour un opérateur humain : peinture ou soudage des carrosseries automobiles. Aujourd'hui, l'évolution de l'électronique et de l'informatique permet de développer des robots plus précis, plus rapides ou avec une meilleure autonomie. Industriels, militaires ou spécialistes chirurgicaux rivalisent d'inventivité pour mettre au point des robots assistants les aidant dans la réalisation de tâches délicates ou dangereuses. Dans le même temps apparaissent des robots à usages domestiques : aspirateur, tondeuses, etc.

QUESTION :

Qui sont les ancêtres de robots ?

REPONSE :

Les ancêtres des robots sont les automates. Un automate très évolué fut présenté par Jacques de Vaucanson en 1738 : il représentait un homme jouant d’un instrument de musique à vent. Jacques de Vaucanson créa également un automate représentant un canard mangeant et refoulant sa nourriture après ingestion de cette dernière.

Vaucansson travailla également sur les métier à tisser pour les automatiser. C’est grâce au cylindre à encoches qu’il a développé pour ses automates, qu’il a pu faire exécuter automatiquement des tissus aux motifs particulier à ces métiers à tisser.

Héron d'Alexandrie au 1er siècle réalisait des automates mus par la vapeur, Léonard de Vinci au seizième siècle en a également réalisé pour ne citer que les plus célèbres. Les horlogers sont des fabricants d'automates.

QUESTION :

Le turc mécanique qu'est-ce que c'est ?

REPONSE :

Le Turc mécanique ou l’automate joueur d'échecs est un célèbre canular construit à la fin du XVIIIe siècle : il s’agissait d'un prétendu automate doté de la faculté de jouer aux échecs.

Il avait l’apparence d'un mannequin habillé d’une cape et d’un turban assis derrière un meuble d’érable qui possédait des portes révélant une mécanique et des engrenages internes qui s'animaient lors de son activation.Ce mécanisme n'était qu'une illusion permettant de masquer un autre compartiment secret du meuble dans lequel un joueur humain pouvait se glisser, et manipuler le mannequin, comme un marionnettiste, sans être vu. L'automate était alors capable de jouer une partie d'échecs contre un adversaire humain. Le Turc mécanique remporta la plupart des parties d'échecs auxquelles il participa en Europe et en Amérique durant près de 84 ans, y compris contre certains hommes d'État tels que Napoléon Bonaparte, Catherine II de Russie et Benjamin Franklin.

QUESTION :

Le turc mécanique d'Amazon, qu'est-ce que c'est ?

REPONSE :

Amazon Mechanical Turk (AMT, en français « Turc mécanique d'Amazon ») est un service de micro-travail lancé par Amazon.com fin 2005. C'est une plateforme web de crowdsourcing qui vise à faire effectuer par des humains, contre rémunération, des tâches plus ou moins complexes. Les tâches en question doivent être dématérialisées ; il s'agit souvent d'analyser ou de produire de l'information dans des domaines où l'intelligence artificielle est encore trop peu performante, par exemple l'analyse du contenu d'images.

les travailleurs (turkers) travaillent à la tâche. Ils seraient entre 15 000 et 43 000. Parmi eux, 20 % considèrent AMT comme leur source de revenu primaire, 50 % comme leur source de revenu secondaire. 20 % des travailleurs passent plus de 15 heures par semaine sur AMT, et contribuent à 80 % des tâches.

Le salaire horaire moyen observé ne dépasse pas les 2$.

QUESTION :

Citez 5 robots de fiction.

REPONSE :

R2D2 et C3PO (star-wars) | Bender le robot de Futurama. | CASE et TARS les robots de Interstellar. | Optimus Prime des films Transformers.
Robby, le robot (du film planète interdite) | Nono (le petit robot de télémaque dans Ulysse 31) | Wall-e et Eva les deux robots du film. | Les réplicants de Blade Runner (deckard en est-il?).
Maria la robote du film métropolis. | Hal 9000 le robots-vaisseau de 2001 l'odyssée de l'espace. | Astro, le robot (du manga animé du même nom). | Les sentinelles de X-men, days of the futur past.
Les Cylons (de Galactica) | Marvin (le robot dépressif de H2G2) | Ash, l'androïde dans Alien | D.A.R.YL. Un androïde enfant.
Les robot pieuvres de Matrix. | Sonny, le robot de « I, Robot » | David, l'androïde de Prometheus. | Gort du film le jour ou la terre s'arrêta.
Terminator | Ava de ex-machina | Chappie | Le grand automate du roi et l'oiseau

QUESTION :

Les lois de la robotique, qu'est-ce que c'est ?

REPONSE :

Exposées pour la première fois dans sa nouvelle « Cercle vicieux » (Runaround, 1942) les lois sont :

1. un robot ne peut porter atteinte à un être humain, ni, en restant passif, permettre qu'un être humain soit exposé au danger ;

2. un robot doit obéir aux ordres qui lui sont donnés par un être humain, sauf si de tels ordres entrent en conflit avec la première loi ;

3. un robot doit protéger son existence tant que cette protection n'entre pas en conflit avec la première ou la deuxième loi.

Une loi zéro, sera instituée par deux robots, mais elle n'est pas codée au niveau matériel des cerveaux positroniques, à la différence des trois premières, c'est une loi de type logiciel, puisque « déduite » par le robot R. Giskard Reventlov.

Loi Zéro : Un robot ne peut pas porter atteinte à l'humanité, ni, par son inaction, permettre que l'humanité soit exposée au danger ;

Asimov considérait que ses lois devaient être universelles pour les robots. Aussi, assistant à la projection de 2001, l'Odyssée de l'espace, il quitta avec bruit la salle lorsque l'ordinateur HAL 9000 viola sa première loi en s'attaquant à des humains. Aujourd'hui rien ne permet de d'obliger un robot à respecter ces lois.

QUESTION :

Qu'est-ce que c'est qu'un cobot ?

REPONSE :

Le mot cobot désigne une catégorie de robots conçus pour une interaction directe avec un opérateur humain, dans un espace de travail partagé. Les cobots présentent plusieurs avantages :

- simplicité de programmation, puisque le robot est dirigé par un humain (en permanence ou bien durant la phase d'apprentissage) ;
- souplesse, capacité à changer d'activité rapidement, pour les mêmes raisons ;
- évite la mise en place d'enceintes sécurisées, les sécurités du cobot étant conçues pour travailler parmi les humains.

QUESTION :

Qu'est-ce que la fabrication dans le noir ?

REPONSE :

La fabrication dans le noir est une approche à la fabrication où les usines sont entièrement automatisées et n'ont besoin d'aucune présence humaine. Ainsi, les usines peuvent fonctionner avec les lumières éteintes, dans le noir. De nombreuses usines sont capables d'une production dans le noir, mais très peu adoptent pleinement cette politique. Typiquement, il faut des ouvriers pour bien disposer les pièces à être travaillées, et enlever les pièces finies. Une usine automatique est un établissement où les matières premières entrent et les produits finis sortent sans (ou avec très peu de) contribution humaine. FANUC, le constructeur japonais de robots, a maintenu une politique d'usines dans le noir depuis 2001. Selon le vice-président Gary Zywiol, des robots construisent d'autres robots à une vitesse de 50 par jour et peuvent continuer sans surveillance jusqu'à 30 jours. Non seulement c'est une usine dans le noir, mais on a éteint la climatisation et le chauffage.

QUESTION :

Les robots prennent-ils le travail des humains ?

REPONSE :

Oui et non. Oui car il sont conçus pour cela : effectuer des taches de manière automatique. C'est le prolongement des outils, cela vise à faciliter la vie. Non car nous ne faisons pas moins de choses, il y a toujours quelque chose à faire (c'est un peu comme à la maison : nettoyer, ranger, décorer, transformer, améliorer, agrandir, …). Le problème avec le travail, c'est que c'est aujourd'hui vu comme la seule manière de répartir les richesses. Les gens sont donc dépendant du travail et quand l'automatisation arrive dans une entreprise ou un secteur d'activité, cela peut détruire des emplois. Ce qui est un drame pour les gens qui dépendent des revenus de cet emplois. Le problème est donc plus un problème de solidarité et de répartition des richesses. Pourtant il y en a plein d'autres manière que le travail pour répartir les richesses et cette répartition est parfois injuste et parfois solidaire : l'héritage, les rentes (location d'immeubles, revenus des capitaux), bénéfices des entreprises, allocation solidaires (revenu minimum, chômage, retraite, handicap, RSA).

QUESTION :

Peut-on pirater les robots ?

REPONSE :

Nous avons réussis à pirater ces robots de multiples façons. Cela nous a permis de confirmer notre hypothèse de départ : il est urgent de prendre des mesures immédiates pour sécuriser les robots. Les fournisseurs privilégient la mise sur le marché plutôt que les tests de sécurité. Il faudrait prendre en compte la cybersécurité dès le début du cycle de vie du produit.

En 2009, les recherches de l'Université de Washington ont révélé que les robots domestiques ne protègent ni la sécurité, ni la confidentialité des utilisateurs. La cybersécurité des robots ne s'est pas amélioré en près de huit ans, et, en fait, aujourd'hui c’est pire.

Heureusement, l'adoption des robots n’étant pas encore massive, il est encore temps d'améliorer la technologie et la rendre plus sûre.

Si nous combinons une puissante technologie d'Intelligence Artificielle en plein essor avec des robots peu sûrs, le scénario de Skynet des célèbres films Terminator ne semble plus aussi loin que ça.

Il faut que les fournisseurs de robots prennent la cybersécurité au sérieux. Si l’écosystème des robots continuent à être vulnérables au piratage, les robots pourraient bientôt finir par nous blesser au lieu de nous aider, et potentiellement supprimer la «fiction» de la science-fiction.

Publication : "Hacking Robots Before Skynet" – février 2017 – par Cesar Cerrudo et Lucas Apa de l'équipe de recherche en cyber-sécurité de l'entreprise IOActive.

QUESTION :

L'intelligence artificielle qu'est-ce que c'est ?

REPONSE :

L'intelligence artificielle est "l'ensemble de théories et de techniques mises en œuvre en vue de réaliser des machines capables de simuler l'intelligence". L'intelligence artificielle correspond à un ensemble de concepts et de technologies plus qu'à une discipline autonome constituée. Elle recherche des méthodes de résolution de problèmes à forte complexité logique ou algorithmique. Par extension elle désigne, dans le langage courant, les dispositifs imitant ou remplaçant l'humain dans certaines mises en œuvre de ses fonctions cognitives.

Ses finalités et son développement suscitent, depuis toujours, de nombreuses interprétations, fantasmes ou inquiétudes s'exprimant tant dans les récits ou films de science-fiction que dans les essais philosophiques. Historiquement, elle trouve son point de départ avec les travaux de Alan Turing qui se demande en 1950 si une machine peut « penser ». Le développement récent des technologies informatiques et des techniques algorithmiques comme le deep learning et les réseaux neuronaux ont permis la réalisation de programmes informatiques surpassant l'homme dans certaines de ses capacités cognitives emblématiques : le jeu d'échecs en 1997, le jeu de go en 2016 et le poker en 2017. Ces succès encouragent les spéculations. Dans les milieux technophiles, on verse en général dans l'enthousiasme, le mouvement transhumaniste en est la meilleure expression. Au contraire, d'autres s’inquiètent et sont portées par une perplexité, parfois alarmiste, y compris dans la sphère de la haute technologie.

QUESTION :

Qu'est-ce le test de Turing ?

REPONSE :

Le test de Turing est une proposition de test d’intelligence artificielle fondée sur la faculté d'une machine à imiter la conversation humaine. Décrit par Alan Turing (mathématicien anglais) en 1950 dans sa publication Computing machinery and intelligence, ce test consiste à faire un humain discuter par écrit à l’aveugle avec un ordinateur et un autre humain.

Si la personne qui engage les conversations n’est pas capable de dire lequel de ses interlocuteurs est un ordinateur, on peut considérer que le logiciel de l’ordinateur a passé avec succès le test. Cela sous-entend que l’ordinateur et l’humain essaieront d’avoir une apparence sémantique humaine.

Dans la publication de Turing, le terme « Jeu d’imitation » est utilisé pour sa proposition de test. Le nom de « Test de Turing » semble avoir été inventé en 1968 par le romancier britannique Arthur C. Clarke dans ses nouvelles de science-fiction dont a été tiré le film 2001, l'Odyssée de l'espace.

QUESTION :

Comment s'appelle le premier programmeur de l'histoire ?

REPONSE :

Ce programmeur est une programmeuse, il s'agit d'ADA Lovelace (XIXième siècle 1815 à 1852).

C'est une pionnière de la science informatique. Elle est principalement connue pour avoir réalisé le premier programme informatique, lors de son travail sur un ancêtre de l'ordinateur : la machine analytique de Charles Babbage.

Dans ses notes, on trouve en effet le premier algorithme publié et destiné à être exécuté par une machine. Elle a également entrevu et décrit certaines possibilités offertes par les calculateurs universels, allant bien au-delà du calcul numérique et de ce qu'imaginaient ses contemporains.

De nombreux développeurs connaissent le langage Ada, nommé en son honneur.

QUESTION :

Qu'est-ce qu'un cyborg ?

REPONSE :

Un cyborg (de l'anglais « cybernetic organism », traduisible par « organisme cybernétique ») est un être humain — ou à la rigueur un autre être vivant intelligent, en science-fiction — qui a reçu des greffes de parties mécaniques.

Le terme s'emploie surtout en science-fiction ou en futurologie ; utiliser le terme pour des personnes ayant reçu des prothèses, dans le monde contemporain, peut parfois être perçu comme de mauvais goût par les intéressés.

QUESTION :

Son petit nom c'est R2, qui est le robot Robonaute 2 ?

REPONSE :

Robonaut 2 est un robot humanoïde né du Programme Robonaut. Un exemplaire a été livré par la navette spatiale Discovery en février 2011 dans le but de voir la manière dont le robot fonctionne en apesanteur.

Robonaut 2 a été conçu dans le but d'aider le travail des astronautes dans des situations délicates, notamment lors de sorties extravéhiculaires. Cela permettra aussi de diminuer considérablement le risque de pertes humaines.

Robonaut 2 est un robot de forme humanoïde dont la silhouette évoque un astronaute dans sa combinaison spatiale. Il pèse 136 kilos et son envergure est de 2,4 mètres, une fois ses bras déployés. Chaque bras est capable de soulever jusqu'à 9 kilogrammes. Les mains du robot disposent de 14 degrés de liberté et ses doigts possèdent 4 articulations. Le robot contient de plus de nombreux capteurs sensoriels.

QUESTION :

Pour quelle raison souhaite-t-on fabriquer des robots humanoïdes ?

REPONSE :

Un robot humanoïde est, par définition, extrêmement bien adapté à l'environnement humain. Il pourra donc réaliser toutes les taches que peuvent faire les humains. C'est aussi à cause de cela que certains concepteurs de robots préfèrent fabriquer des robots qui sont adapater à leurs taches plutôt que de ressembler à un humain.

QUESTION :

Qu'est-ce que la vallée de l'étrange ?

REPONSE :

La vallée dérangeante, ou vallée de l'étrange (de l'anglais uncanny valley) est une théorie scientifique du roboticien japonais Masahiro Mori, publiée pour la première fois en 1970, selon laquelle plus un robot androïde est similaire à un être humain, plus ses imperfections nous paraissent monstrueuses. Ainsi, beaucoup d'observateurs seront plus à l'aise en face d'un robot clairement artificiel que devant un robot doté d'une peau, de vêtements et d'un visage visant à le faire passer pour humain. Ce n'est qu'au-delà d'un certain degré de réalisme dans l'imitation; selon cette théorie, que les robots humanoïdes seront mieux acceptés. C'est pour cela qu'est utilisé le terme de vallée : il s'agit d'une zone à franchir dans laquelle chaque progrès fait vers l'imitation humaine amènera au départ plus de rejet, mais passé un certain seuil de réalisme une acceptation plus grande. Cependant, ce n'est qu'une théorie sujette à critique !

QUESTION :

Citez le nom de 3 robots réels ?

REPONSE :

Nao le robot d'Aldebaran robotics (Pepper et Roméo aussi) | Reem le robot policier humanoïde mis en service de à Dubaï. | Les robots allemands KUKA, industriels sur les chaines de montage auto
Robot de sécurité K5 de KnightScope qui est tombé dans une fontaine. | Les robots de Boston Dynamics : Petman, Atlas, Cheetah, SandFlea, Rise, Big Dog, Handle, Spot-mini, | Les voitures Tesla motors qui conduisent seule (sur voie express uniquement et sous la surveillance d'un humain).
Rosa, robot d'assistance à la neuro-chirurgie. | Baxter, le cobot de Rethink Robotics. | B.A.R.Y.L, le robot poubelle de la gare de Lyon.
Les robots BettyBot des entrepôts d'Amazon | Swing-bot, le robot laveur de sol de la gare de Lyon | Roomba, les célèbres robots aspirateurs.
Asimo, le robot de Honda | Robonaut 2 de la NASA
Le VAL (Véhicule Automatique Léger) métro automatique à Rennes, Toulouse, Orly, Lille... | Les cobots UR5 d'Universal Robotics

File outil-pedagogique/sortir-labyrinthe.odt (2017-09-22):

## Sortir du labyrinthe !

Dans cet exemple, nous allons utiliser SNAP pour programmer le petit bot et ainsi le faire sortir du labyrinthe.

Matériel :

- 8 petits bot version basique
- Des obstacles
- 8 ordinateurs
- Une règle / Un rapporteur
- Le logiciel SNAP!

Programmer les fonctions du petit bot :

Dans cette première séquence, nous allons créer la fonction « avance » qui aura pour effet de faire avancer le petit bot de 5 cm.

Avant de se lancer dans la programmation, prendre un temps à imaginer la fonction, quelles sont les actions à réaliser pour faire avancer le petit bot et faire en sorte qu’il s’arrête net ?

3 commandes seront nécessaires : Avancer / Attendre / Stopper

Il est tout à fait possible de mimer le déplacement du petitbot (robot idiot) en chronométrant le déplacement et en mesurant celui-ci avec un mètre.

Déplacer le petitbot avec Snap !

Démarrez snap ! Et commencez à créer 2 variables « avancer » et « stopper »


En bas de la catégorie variable, cliquer sur le bouton « nouveau bloc » pour créer la fonction « avance »

Ici nous choisissons « commande » puis nous sélectionnons dans quelle catégorie va se retrouver notre fonction « avance ».

Une fenêtre permettant de créer un script s’ouvre, c’est ici que nous allons ajouter des blocs :


Une fois validé sur OK, vous disposez d’un nouveau bloc « avance ».

voici un exemple d’utilisation :


Pour le modifier, il suffit de faire un clique droit dessus, puis éditer.

Étalonner le petit bot

Une fois que vous avez réalisé la fonction avance, appuyez sur espace et observez la distance parcourue par le petit bot.

- Quel outil et quelle variable allons nous utiliser pour faire en sorte que le Petitbot parcours 5 cm lorsque l’on appuie sur la touche espace ?

Sortir du labyrinthe

Après avoir réalisé et étalonné tous les blocs fonctions nécessaires au pilotage de petitbot, il est temps de tester la sortie du labyrinthe !

Le petit Bot - 2017


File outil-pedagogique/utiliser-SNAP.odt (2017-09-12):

## Contrôler le petit Bot avec SNAP!


Le principe d'un programme SNAP! pour le petit Bot.

SNAP! contrôle le petit bot tout comme vous si il cliquait sur la page Web du petit Bot.

Pour cela, il appelle l'URL souhaitée en faisant qu'une variable « prend la valeur » d'un capteur http:// dans lequel on aura inscrit l'URL http://192.168.4.1/avance par exemple


Exercice pratique, ouvrez SNAP!

Créez une variable « action » par exemple.


Puis prenez le bloc prend la valeur


Puis prenez un bloc http:// en y mettant l'URL :

192.168.4.1/avance


puis prener un bloc de contrôle quand une touche est pressée

Et voici un bloc qui fait avancer le petit bot lorsqu'on appuie sur la touche « flèce haut ».

Répétez l'opération pour toutes les commandes et vos obtenez une télécommande à petit Bot !


Le petit Bot - 2017

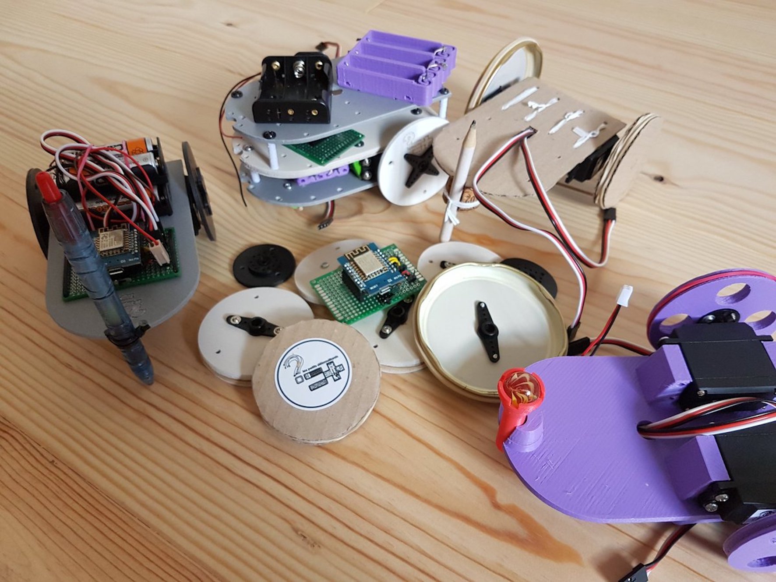
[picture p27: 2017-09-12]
images/diversite-petits-bots/petitsbots-divers.jpg

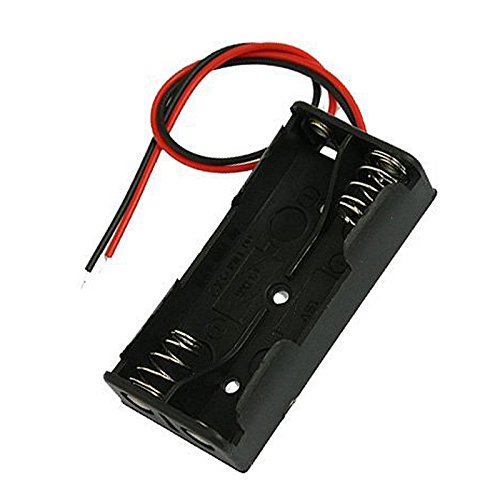
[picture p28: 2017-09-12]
images/composants-electroniques/support2piles.jpg

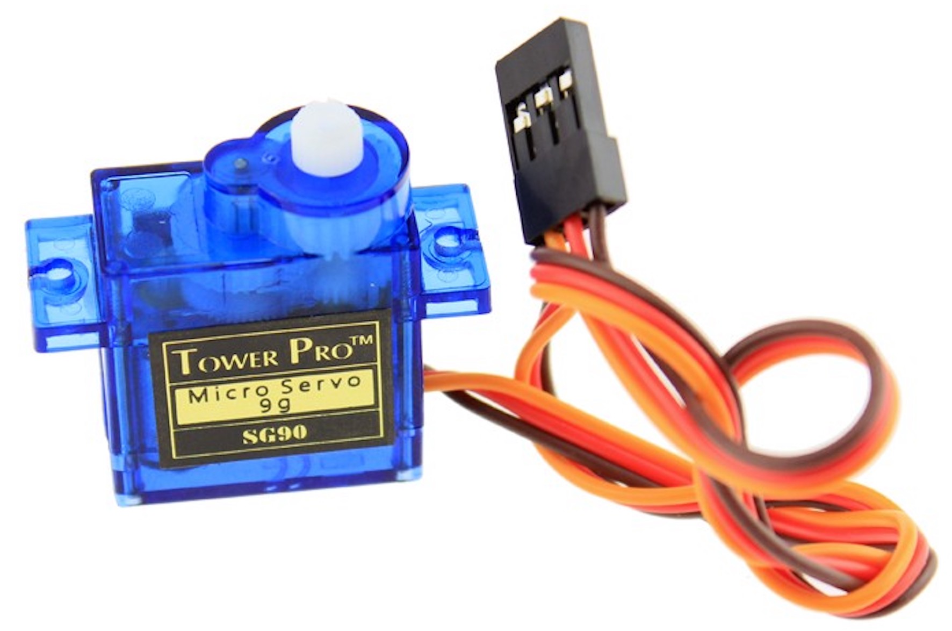
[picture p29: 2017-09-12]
images/composants-electroniques/photoservo9G.jpg

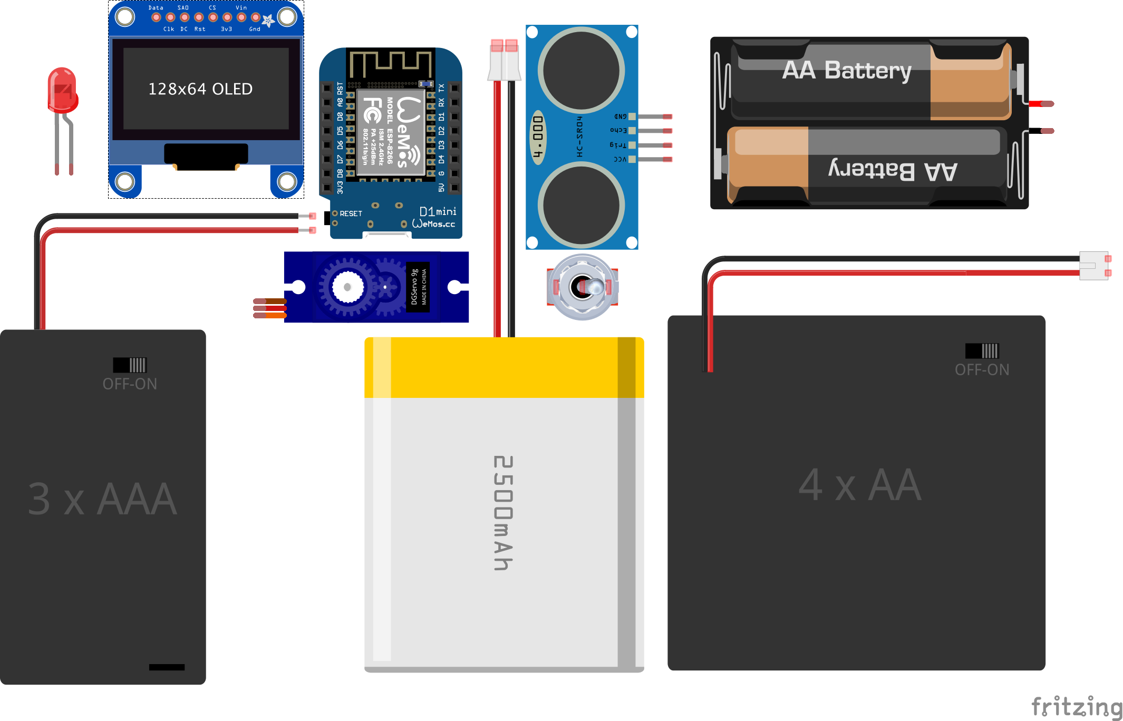
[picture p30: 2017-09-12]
images/composants-electroniques/composantsindividuels_bb.png

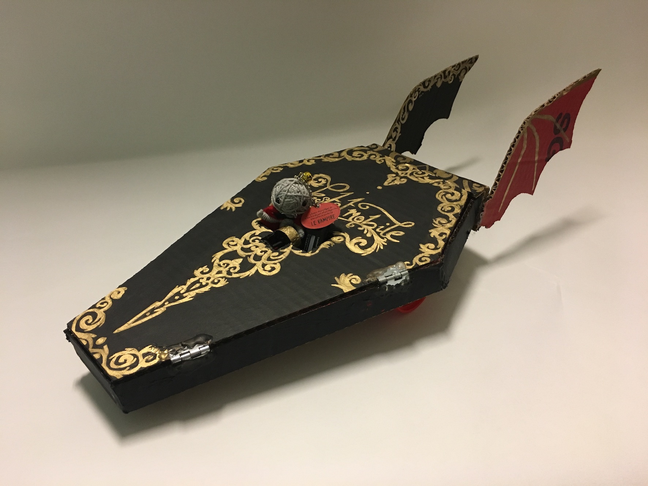
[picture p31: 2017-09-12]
images/diversite-petits-bots/petitbot-lestatmobile.JPG

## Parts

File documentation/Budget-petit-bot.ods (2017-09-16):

désignation | quantité | prix livraison incluse | prix unitaire | liens
cables dupont - « jumper » - male-male | 400 | 10,16 € | 0,51 € | https://fr.aliexpress.com/item/40pcs-dupont-cable-jumper-wire-dupont-line-male-to-male-dupont-line-20cm-1P-diameter-2/32481603887.html
Cables USB Data | 20 | 11,46 € | 0,57 € | https://fr.aliexpress.com/item/10pcs-lot-Top-Micro-Usb-Cable-Mini-1M-Flat-Noodle-Micro-USB-Data-Sync-Charger-Microusb/32358865341.html
bobines de fils électrique | 2 | 4,74 € | 0,24 € | https://fr.aliexpress.com/item/10-Meters-Ul758-2000-Electronic-Wire-18awg-1mm-Pvc-Electronic-Wire-Electronic-Cable-Ul-Certification-18/32744949817.html
interrupteurs | 20 | 3,98 € | 0,20 € | https://fr.aliexpress.com/item/20Pcs-SPDT-ON-ON-2-Positions-3-Pin-Latching-Micro-Toggle-Switch-MTS-102/32666699769.html
Plaques de prototypage | 10 | 3,25 € | 0,33 € | https://fr.aliexpress.com/item/10pcs-lot-Syb-170-Tie-points-Mini-Solderless-Prototype-Breadboard-for-ATMEGA-PIC-Arduino-UNO-Wholesale/1968046374.html
Plaques de prototypage | 10 | 3,26 € | 0,33 € | https://fr.aliexpress.com/item/10pcs-lot-Syb-170-Tie-points-Mini-Solderless-Prototype-Breadboard-for-ATMEGA-PIC-Arduino-UNO-Wholesale/1968046374.html
batterie | 20 | 88,00 € | 4,40 € | https://fr.aliexpress.com/item/2600mAh-5V-Small-Light-Weight-Portable-Power-Bank-External-Battery-Charger-Poverbank-For-Mobile-For-iPhone/32815374430.html
Servomoteurs | 40 | 134,86 € | 6,74 € | https://fr.aliexpress.com/item/50pcs-lot-DM-S0090D-R-9g-0-08s-1-8kg-digital-micro-servo-360degree-continuous-rotation/32657400075.html
wemos D1 Mini | 20 | 49,24 € | 2,46 € | https://fr.aliexpress.com/item/10PCS-D1-mini-Mini-NodeMcu-4M-bytes-Lua-WIFI-Internet-of-Things-development-board-based-ESP8266/32705442691.html
TOTAL |  | 308,95 € | 15,77 €
Soient | 15,45 € | par petit bot, pour 20

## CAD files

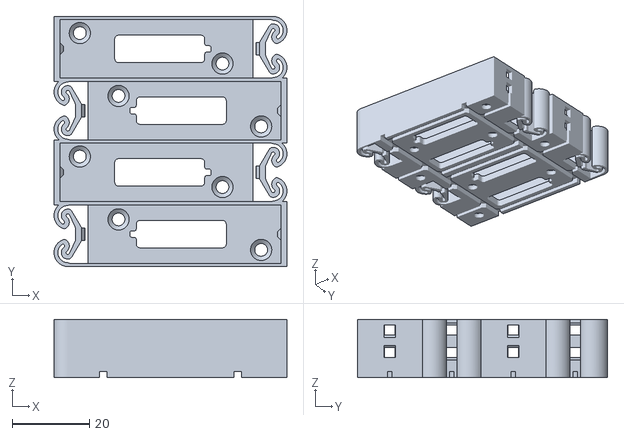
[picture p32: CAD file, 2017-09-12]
impressions_3D/BattHolder-4AA.stl
60.4 x 64.8 x 15.1

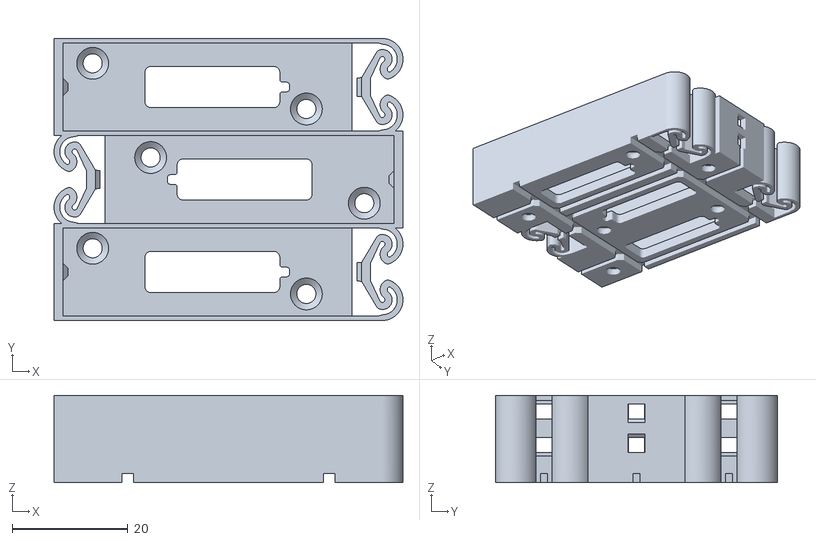
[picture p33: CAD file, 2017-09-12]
impressions_3D/BattHolder-3AA.stl
60.4 x 48.8 x 15.1

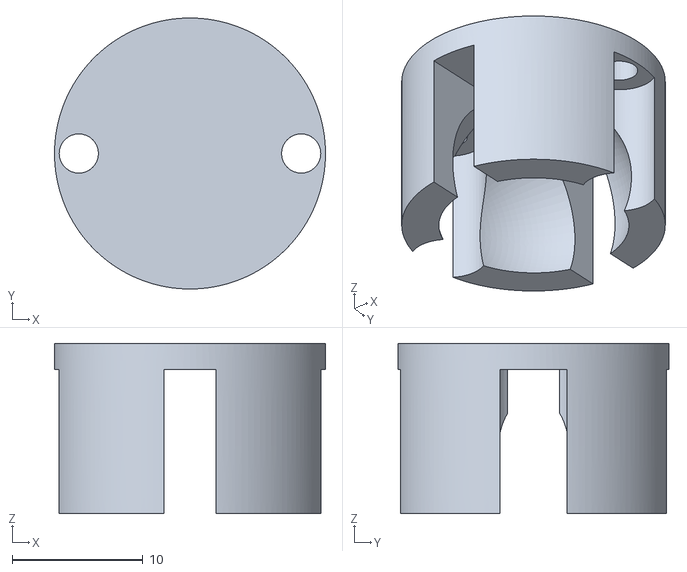
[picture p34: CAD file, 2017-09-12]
impressions_3D/Petitbot-roue-bille.stl
20.7 x 20.7 x 13.0

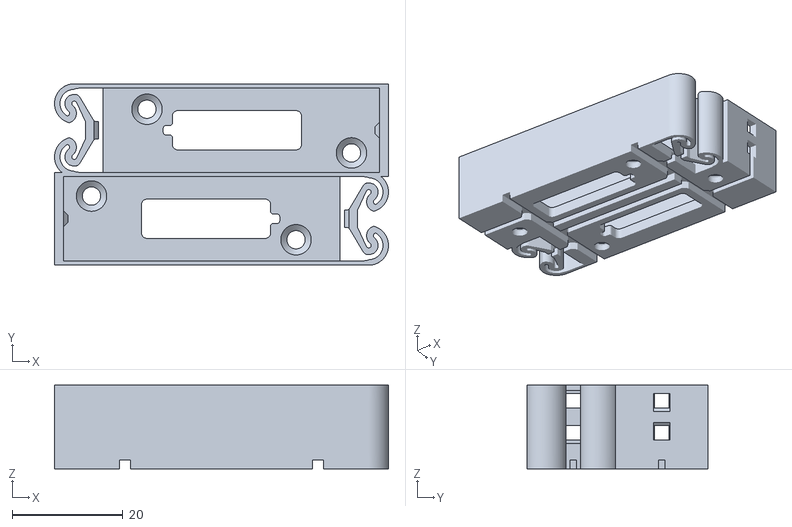
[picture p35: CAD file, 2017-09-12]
impressions_3D/BattHolder-2AA.stl
60.4 x 32.8 x 15.1

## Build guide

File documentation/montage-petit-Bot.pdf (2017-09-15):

# Montage du petit Bot

Le montage de base
Liste du matériel :
- 1 wemos D1 mini.
- 2 servomoteurs à rotation continue
- 1 batterie 5V
- 1 interrupteur
- 8 fils dupont : 1 jaune, 1 vert, 3 rouges, 3 noirs.

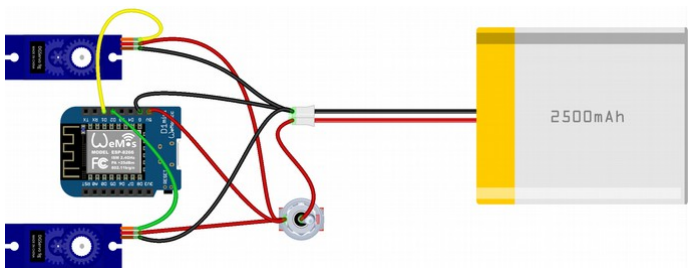
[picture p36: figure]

Le schéma paraît touffu car il y a 8 fils qui se recouvrent. Aussi pour comprendre le schéma, il faut mettre de l'ordre (on place l'interrupteur sur le + de la batterie) :
- Du + (interrupteur) : 3 fils rouges vers chaque composant pour les alimenter.
- Du - : 3 fils noirs vers chaque composants.
- De la broche D1 du Wemos au servo gauche : un fil jaune.
- De la broche D2 du Wemos au servo droit : un fil ver

Comment faire les roues ?
1 – récupérer des choses circulaires :
- bouchons de bouteilles variées
- couvercles de pots divers
- …
2 – découper des matériaux
- Gros carton ondulé
- autre...
3 – les coller sur les servomoteurs :
Les servomoteurs sont livrés avec des accessoires qui se fixent sur l'axe avec la plus petite des 3 vis fournies. Prenez soin de bien visser un de ces accessoires qui couvre de préférence un diamètre (en croix, en disque ou en transversal simplement). Cela ajoute à la rigidité de votre roue.

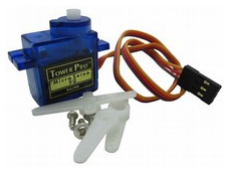
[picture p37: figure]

Comment faire le châssis ? Inspirez-vous des photos et inventez !

# Le petit Bot - 2017

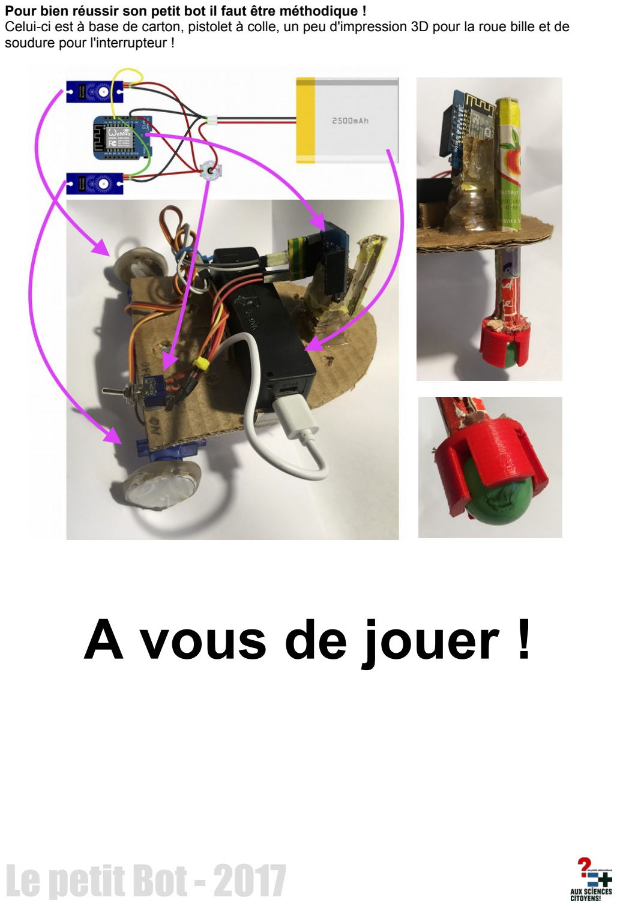
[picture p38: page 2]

Pour bien réussir son petit bot il faut être méthodique !
Celui-ci est à base de carton, pistolet à colle, un peu d'impression 3D pour la roue bille et de soudure pour l'interrupteur !

# A vous de jouer !

# Le petit Bot - 2017

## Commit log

2017-08-29 menus changements
    [PETITBOT.fzz]
2017-09-13 maj Robot Quizz : les questions
2017-09-16 ajout du budget
    [Budget-petit-bot.ods]
2017-12-13 Mise à jour
    Multiple
    [composants-petit-bot.fzz, shema-petit-bot-battery5V-sans-cables.fzz, shema-petit-bot-decompose-controles.fzz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]
2021-07-08 Update petitbot.ino
    Correction de l'erreur des broches d'attache des servos
    [petitbot.ino]
